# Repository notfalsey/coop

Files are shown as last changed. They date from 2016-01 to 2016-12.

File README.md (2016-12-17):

# coop
This project includes the Arduino sketch and Fritzing schematic for a chicken coop controller.  The controller opens and shuts the door based on input from remote i2c commands or local override toggle switches.  The schematic does not include the i2c wiring yet.  

Some of the ideas were taken from the implementation here http://davenaves.com/blog/interests-projects/chickens/arduino-chicken-coop/ .  I originally started with a light controlled coop using input from the photo resistor like Dave did, but I went through two photo resistors that were giving bad readings.  I tried insulating them with different materials including silicone and glass food jars, but could not get them to work reliably.  Also, there is the minor problem of artificial light like car head lamps, which is usually temporary though.  So, I changed my design to have a raspberry pi master in my crawl space driving the arduino controller slave over i2c based on local sunrise/sunset retrieved from the weatherundergroud REST API.  i2c is designed for short distance board-to-board commmunication, but it still works nicely if you use low capacitance wires like cat 5.  And it is so nice to communicate using just three wires including the common ground wire.  I originally used water sprinkler wire but the capacitance was too high for i2c at a distance of 25 ft, so I switched to cat 5.  The really nice thing about using the raspberry pi master is I can control and monitor the coop remotely.  I have a web server running on the raspberry pi which allows me to monitor and control the coop while I am away.  The source for the web application that acts as the i2c master is at https://github.com/notfalsey/cooperator

This sketch also utilizes a watchdog timer to reset the arduino under the following conditions:
- there is something causing the main loop to hang
- there is a remote reset command sent from the master i2c device
- there has not been any command within the timeout (currently set at 5 minutes)

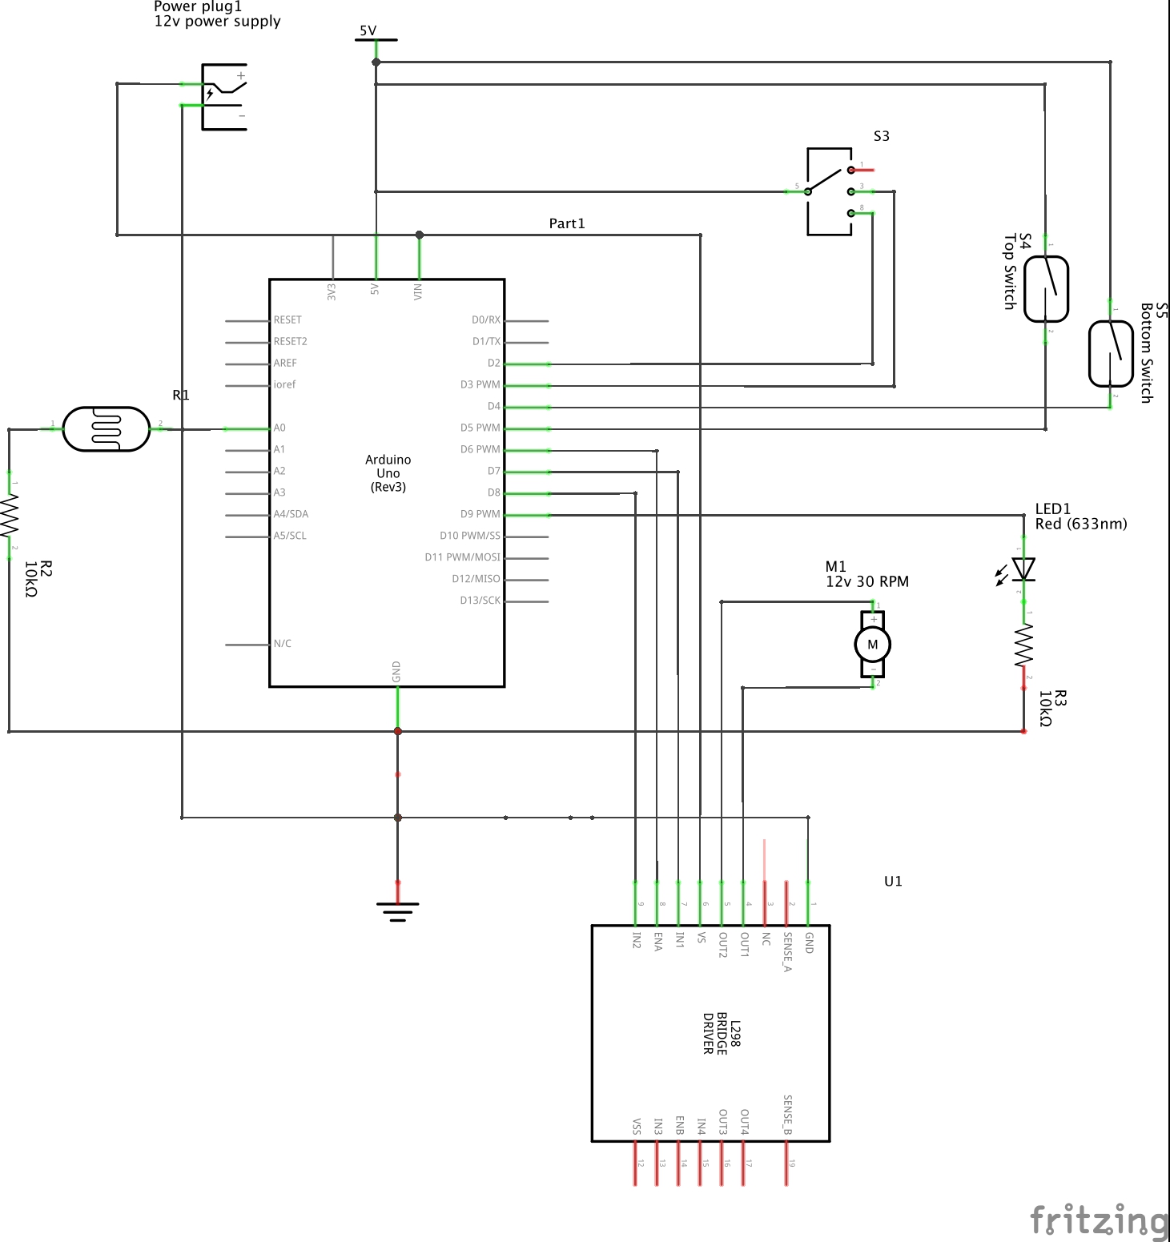
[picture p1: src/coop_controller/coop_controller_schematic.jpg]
Coop Controller Schematic


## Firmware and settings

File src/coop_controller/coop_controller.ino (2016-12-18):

#include <Wire.h>
#include <avr/wdt.h>

#define DEBUG

#ifdef DEBUG
 #define DEBUG_PRINTLN(x) Serial.println(x)
 #define DEBUG_PRINT(x) Serial.print(x)
#else
 #define DEBUG_PRINTLN(x)
 #define DEBUG_PRINT(x)
#endif

// pin assignments
const int PHOTO_CELL_PIN = A0; 
const int TEMP_PIN = A1;
const int OVERRIDE_SWITCH_PIN = 2;
const int OVERRIDE_DIR_PIN = 3;
const int BOTTOM_SWITCH_PIN = 4;    
const int TOP_SWITCH_PIN = 5;       
const int ENABLE_MOTOR_PIN = 6;     
const int CLOSE_MOTOR_PIN = 7;  
const int OPEN_MOTOR_PIN = 8;   
const int CLOSED_LED_PIN = 9;

// I2C bus address
#define SLAVE_ADDRESS 0x05

// command constants
const unsigned long COMMAND_TIMEOUT = 60 * 1000; // 1 minute
const byte CMD_ECHO = 0;
const byte CMD_RESET = 1;
const byte CMD_READ_TEMP = 2;
const byte CMD_READ_LIGHT = 3;
const byte CMD_READ_DOOR = 4;
const byte CMD_SHUT_DOOR = 5;
const byte CMD_OPEN_DOOR = 6;
const byte CMD_AUTO_DOOR = 7;
const byte CMD_UPTIME = 8;
const byte CMD_READ_MODE = 9;

// global variables
bool remoteClose = false;
bool remoteOpen = false;
bool resetRequested = false;

const int RESPONSE_SIZE = 4;
byte response[RESPONSE_SIZE]; 

unsigned long lastCommandTime = millis();
unsigned long DEBOUNCE_DELAY = 100;

#define AREF_VOLTAGE 5.0

// ************************************** the setup **************************************

void setup(void) {
  Serial.begin(9600); // initialize serial port hardware
  DEBUG_PRINTLN("Coop Controller starting...");
  
  // coop door motor
  pinMode (ENABLE_MOTOR_PIN, OUTPUT);  // enable motor pin = output
  pinMode (CLOSE_MOTOR_PIN, OUTPUT);   // motor close direction pin = output
  pinMode (OPEN_MOTOR_PIN, OUTPUT);    // motor open direction pin = output
  stopCoopDoorMotor();
 
  // coop door leds
  pinMode (CLOSED_LED_PIN, OUTPUT);        // enable coopDoorClosedLed = output
  digitalWrite(CLOSED_LED_PIN, LOW);
 
  // coop door override switches
  pinMode (OVERRIDE_SWITCH_PIN, INPUT);
  digitalWrite(OVERRIDE_SWITCH_PIN, LOW);
  pinMode (OVERRIDE_DIR_PIN, INPUT);
  digitalWrite(OVERRIDE_DIR_PIN, HIGH);
 
  // bottom switch
  pinMode(BOTTOM_SWITCH_PIN, INPUT);       // set bottom switch pin as input
  digitalWrite(BOTTOM_SWITCH_PIN, HIGH);   // activate bottom switch resistor
 
  // top switch
  pinMode(TOP_SWITCH_PIN, INPUT);          // set top switch pin as input
  digitalWrite(TOP_SWITCH_PIN, HIGH);      // activate top switch resistor

  DEBUG_PRINTLN("Joining i2c bus...");
  Wire.begin(SLAVE_ADDRESS);

  Wire.onReceive(onReceive);
  Wire.onRequest(onRequest);

  DEBUG_PRINTLN("i2c ready.");

  setupWatchdog();

  DEBUG_PRINTLN("Coop Controller ready.");
}

// ******** watchdog timer setup **********
void setupWatchdog(void) {
  DEBUG_PRINTLN("Setting up watchdog timer ...");
  cli();
  wdt_reset();
  // Enter Watchdog Configuration mode:
  WDTCSR |= (1<<WDCE) | (1<<WDE);
  // Configure watchdog:
  WDTCSR  = (0<<WDIE)|(1<<WDE)|(1<<WDP3)|(0<<WDP2)|(0<<WDP1)|(1<<WDP0);
  sei();
  DEBUG_PRINTLN("Watchdog timer set.");
}
 
// ************************************** functions **************************************
int isDoorOpen() {
  static int switchState = digitalRead(TOP_SWITCH_PIN);
  static unsigned long lastDebounceTime = millis();
  int reading = digitalRead(TOP_SWITCH_PIN);
  static int lastReading = reading;

  if(reading != lastReading) {
    DEBUG_PRINTLN("Diff reading");
    lastDebounceTime = millis();    
  }

  if ((millis() - lastDebounceTime) > DEBOUNCE_DELAY) { 
    if(reading != switchState) {
      switchState = reading;
      if(switchState == 0) {
        DEBUG_PRINTLN("Top switch CLOSED");
      } else {
        DEBUG_PRINTLN("Top switch OPENED");
      }
    }
  }
  
  lastReading = reading;
  return switchState == 0;
}

int isDoorClosed() {
  static int switchState = digitalRead(BOTTOM_SWITCH_PIN);
  static unsigned long lastDebounceTime = millis();
  int reading = digitalRead(BOTTOM_SWITCH_PIN);
  static int lastReading = reading;

  if(reading != lastReading) {
    DEBUG_PRINTLN("Diff reading");
    lastDebounceTime = millis();    
  }

  if ((millis() - lastDebounceTime) > DEBOUNCE_DELAY) { 
    if(reading != switchState) {
      switchState = reading;
      if(switchState == 0) {
        DEBUG_PRINTLN("Bottom switch CLOSED");
      } else {
        DEBUG_PRINTLN("Bottom switch OPENED");
      }
    }
  }
  
  lastReading = reading;
  return switchState == 0;
}
 
// stop the coop door motor
void stopCoopDoorMotor() {
  //DEBUG_PRINTLN("Stopping motor");
  digitalWrite (CLOSE_MOTOR_PIN, LOW);      // turn off motor close direction
  digitalWrite (OPEN_MOTOR_PIN, LOW);       // turn on motor open direction
  digitalWrite (ENABLE_MOTOR_PIN, LOW);     // disable motor
}
 
// close the coop door motor (motor dir close = clockwise)
void closeCoopDoor() {
  const unsigned long RUN_AFTER_DOWN = 6000; 
  static boolean prevDoorClosed = false;
  static unsigned long timeClosed = 0;
  boolean doorWasClosed = true;
  boolean doorIsClosed = isDoorClosed();
  unsigned long currentTime = millis();
  
  
  if(doorIsClosed && !prevDoorClosed) {
    timeClosed = currentTime;
    DEBUG_PRINT("Set time closed: ");
    DEBUG_PRINTLN(timeClosed);
  }
  if(!doorIsClosed) {
    doorWasClosed = false;
    digitalWrite (CLOSE_MOTOR_PIN, HIGH);     // turn on motor close direction
    digitalWrite (OPEN_MOTOR_PIN, LOW);       // turn off motor open direction
    digitalWrite (ENABLE_MOTOR_PIN, HIGH);    // enable motor
  }
  // if bottom reed switch is closed for enough time 
  // to let slack out of rope and allow levers to lock
  // but only if the controller has not just started otherwise 
  // the motor will run in the down direction at start up 
  // after it is already down and locked
  boolean justStarted = currentTime < (RUN_AFTER_DOWN + 1000);
  boolean hasAllowedSlack = (currentTime - timeClosed) > RUN_AFTER_DOWN;
  if (doorIsClosed && (hasAllowedSlack || justStarted)) {
    stopCoopDoorMotor();
    if(!doorWasClosed && !justStarted) { // we just now closed it
        DEBUG_PRINTLN("Coop Door Closed");
        DEBUG_PRINT("Time since closed: ");
        DEBUG_PRINTLN(currentTime - timeClosed);
    }
  }
  prevDoorClosed = doorIsClosed;
}
 
// open the coop door (motor dir open = counter-clockwise)
void openCoopDoor() {
  boolean doorWasOpen = true;
  boolean doorIsOpen = isDoorOpen();
  
  if(!doorIsOpen) {
    doorWasOpen = false;
    //DEBUG_PRINTLN("Activating motor in open direction");
    digitalWrite(CLOSE_MOTOR_PIN, LOW);       // turn off motor close direction
    digitalWrite(OPEN_MOTOR_PIN, HIGH);       // turn on motor open direction
    digitalWrite(ENABLE_MOTOR_PIN, HIGH);     // enable motor
  }
  if (doorIsOpen) {                    // if top reed switch is closed
    stopCoopDoorMotor();
    if (!doorWasOpen) {
      DEBUG_PRINTLN("Coop Door open");
    }
  }
}

// true if in override mode; false otherwise
boolean isOverrideMode() {
  static boolean lastValue = false;
  boolean newValue = digitalRead(OVERRIDE_SWITCH_PIN) == 1;
  if(lastValue != newValue) {
    if(newValue == true) {
      DEBUG_PRINTLN("Override mode changed to ON");  
    } else {
      DEBUG_PRINTLN("Override mode changed to OFF");  
    }
  }
  lastValue = newValue;
  return newValue;
}

// true if override toggle switch is down; false otherwise
boolean isOverrideDirToggleUp() {
  static boolean lastValue = false;
  boolean newValue = digitalRead(OVERRIDE_DIR_PIN) == 1;
  if(lastValue != newValue) {
    if(newValue == true) {
      DEBUG_PRINTLN("Override toggle direction changed to UP");  
    } else {
      DEBUG_PRINTLN("Override toggle direction changed to DOWN");  
    }
  }
  lastValue = newValue;
  return newValue;
}
 
// do the coop door
void doCoopDoor() {
  static int overrideDirUp = isOverrideDirToggleUp();
  
  if(isOverrideMode()) {
    if(isOverrideDirToggleUp()) {
      openCoopDoor();   
    } else {
      closeCoopDoor();  
    }
  } else if(remoteOpen) {
    openCoopDoor();  
  } else if(remoteClose) {
    closeCoopDoor();   
  }
  if(isDoorClosed()) {
    digitalWrite(CLOSED_LED_PIN, HIGH);
  } else {
    digitalWrite(CLOSED_LED_PIN, LOW);
  }
}
 
// ************************************** the loop **************************************
 
void loop() {
  doCoopDoor();
}

void setResponse(unsigned long number) {
  DEBUG_PRINT("Sending ");
  response[0] = number >> 24;
  DEBUG_PRINT(response[0]);
  DEBUG_PRINT(",");
  response[1] = (number >> 16) & 0x000000FF;
  DEBUG_PRINT(response[1]);
  DEBUG_PRINT(",");
  response[2] = (number >> 8) & 0x000000FF;
  DEBUG_PRINT(response[2]);
  DEBUG_PRINT(",");
  response[3] = number & 0x000000FF;
  DEBUG_PRINTLN(response[3]);
}

void handleEchoCommand(int bytesToRead) {
  if(bytesToRead > RESPONSE_SIZE) {
    DEBUG_PRINTLN("Error requested too many bytes");
  } else {
    for(int i = 0; i < bytesToRead; i++) {
      response[i] = Wire.read();
    }
  }
}

void handleResetCommand() {
  // send response first before we reset
  setResponse(0);
  delay(1000);
  resetRequested = true;
}

void handleReadTempCommand() {
  unsigned long reading = analogRead(TEMP_PIN);
  float voltage = reading * AREF_VOLTAGE / 1024.0;
  float celsius = (voltage - 0.48) * 100;
  float fahrenheit = celsius * 1.8 + 32.0; 
  DEBUG_PRINT("Read ");
  DEBUG_PRINTLN(reading);
  DEBUG_PRINT("Volts: ");
  DEBUG_PRINT(voltage);
  DEBUG_PRINT(", Celsius: ");
  DEBUG_PRINT(celsius);
  DEBUG_PRINT(", Fahrenheit: ");
  DEBUG_PRINTLN(fahrenheit);
  setResponse(reading);
}

void handleReadLightCommand() {
  unsigned long reading = analogRead(PHOTO_CELL_PIN);
  DEBUG_PRINT("Read ");
  DEBUG_PRINTLN(reading);
  setResponse(reading);
}

void handleReadDoorCommand() {
  // use numbers for door state that are unlikely to be transmitted incorrectly (e.g. 0)
  // each state has a single bit set and the possible bit positions are spread out 
  // Three possible states open: 1, transitioning: 8, closed: 64
  // initialize to "in transition"
  unsigned long doorState = 8;
  if(isDoorOpen()) {
    doorState = 1;
  } else if(isDoorClosed()) {
    doorState = 64;
  }
  setResponse(doorState);
}

void handleReadModeCommand() {
  setResponse(isOverrideMode());
}

void handleCloseDoorCommand() {
  remoteClose = true;
  remoteOpen = false;
  setResponse(0);
}

void handleOpenDoorCommand() {
  remoteClose = false;
  remoteOpen = true;
  setResponse(0);
}

void handleAutoDoorCommand() {
  remoteClose = false;
  remoteOpen = false;
  setResponse(0);
}

void handleUptimeCommand() {
  setResponse(millis());
}

void handleCommand(byte command, int bytesToRead) {
    // commands
    
    switch(command) {
      case CMD_ECHO:
         DEBUG_PRINTLN("Received echo command");
         handleEchoCommand(bytesToRead);
         break;
      case CMD_RESET:
         DEBUG_PRINTLN("Received reset command");
         handleResetCommand();
         break;
      case CMD_READ_TEMP:
         DEBUG_PRINTLN("Received read temp command");
         handleReadTempCommand();
         break;
      case CMD_READ_LIGHT:
         DEBUG_PRINTLN("Received read light command");
         handleReadLightCommand();
         break;
      case CMD_READ_DOOR:
         DEBUG_PRINTLN("Received read door command");
         handleReadDoorCommand();
         break;  
      case CMD_SHUT_DOOR:
         DEBUG_PRINTLN("Received close door command");
         handleCloseDoorCommand();
         break;  
      case CMD_OPEN_DOOR:
         DEBUG_PRINTLN("Received open door command");
         handleOpenDoorCommand();
         break;
      case CMD_AUTO_DOOR:
         DEBUG_PRINTLN("Received auto door command");
         handleAutoDoorCommand();
         break;
      case CMD_UPTIME:
         DEBUG_PRINTLN("Received uptime command");
         handleUptimeCommand();
         break;
      case CMD_READ_MODE:
         DEBUG_PRINTLN("Received read mode command");
         handleReadModeCommand();
         break;  
      default: 
        DEBUG_PRINT("Unrecognized command: ");
        DEBUG_PRINTLN(command);
    }
    
    while(Wire.available()) {
      DEBUG_PRINT("Clearing wire data: ");
      DEBUG_PRINTLN(Wire.read());
    }
    
    // we were healthy enough to process an entire command, so reset the watchdog
    if(!resetRequested) {
      wdt_reset(); 
    }
}

void onReceive(int byteCount) {
  DEBUG_PRINT("onReceive byteCount: ");
  DEBUG_PRINTLN(byteCount);
  lastCommandTime = millis();
  if(byteCount > 0 && Wire.available()) {
    handleCommand(Wire.read(), byteCount-1);
  }
}

void onRequest() {
  DEBUG_PRINT("onRequest: sending ");
  int numWritten = Wire.write(response, RESPONSE_SIZE);
}

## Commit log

2016-01-09 Current working version of Arduino coop controller
2016-01-18 Added new commands for remote i2c control
2016-01-31 Add watchdog timer to enable reset command and fix the issue where motor runs down on start up when door is already closed
    [coop_controller.ino]
2016-01-31 Add Fritzing schematic diagram
    [coop_controller.fzz]
2016-01-31 Add image of schematic
2016-01-31 Fix watchdog timer setup Add an uptime command Change response size to 4 bytes to handle unisigned long in uptime command
    [coop_controller.ino]
2016-02-01 Send response back to acknowledge reset commadn before actually resetting
    [coop_controller.ino]
2016-02-04 - Remove light checking logic so controller is entirely driven by remote i2c control or override toggle switches - Also change all serial debug messages to be optionally compiled in/out as these seem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
    [coop_controller.ino]
2016-12-17 Add read override mode command, fix debounce on switches
    [coop_controller.ino]
2016-12-18 Change door states to reduce chance of transmission error, and allow more time for door locks to close with slower motor
    [coop_controller.ino]
